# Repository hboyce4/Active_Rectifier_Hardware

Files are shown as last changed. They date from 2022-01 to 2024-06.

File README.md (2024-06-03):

Design files (Altium) for my bidirectional active rectifier. 

A Cortex-M4-driven bidirectional AC-DC power converter (active rectifier). 300W, 48VDC, 12VAC rms (through mains freq. step-down transformer). It should also be able to absorb/provide AC reactive power too. Its aim is more to be a test platform for control software than a useful/economical PSU. 

As of 2024-06-02, changes have been made to the inverter board but not incorporated into Altium because of a lack of license. They are:
 - PWModulator comparator output has been connected to GPIO PA.10 to measure duty cycle via a timer
 - U17, R56 and C87 have been removed as duty cycle is now measured digitally by a timer
 - R69 and R70 have been changed to 47 Ohm to improve rise time dramatically
 - R74, R76, R79 and R83 have all been changed to 1 Ohm to improve the power MOSFET's turn-off time

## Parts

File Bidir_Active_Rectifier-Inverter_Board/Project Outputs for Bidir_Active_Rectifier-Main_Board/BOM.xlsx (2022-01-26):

Comment | Description | Designator | Footprint | LibRef | Quantity | Value
GCM32EC71H106KA03L | CAP CER 10UF 50V X7S 1210 | C1, C2, C3, C4, C5, C15, C16, C17, C18, C19, C26, C74, C75, C102 | CAPC3225X27N | GCM32EC71H106KA03L | 14
CC0603KPX7R9BB104 | 0603 0.1 uF 50 V ±10% Tolerance X7R SMT Multilayer Ceramic Capacitor | C6, C7, C8, C20, C21, C22, C23, C24, C25, C30, C33, C34, C36, C38, C39, C40, C41, C42, C43, C44, C45, C50, C51, C53, C62, C64, C65, C70, C77, C79, C81, C90, C91, C92, C93, C94, C95, C96, C97, C98, C101, C103, C104, C105, C106, C107, C108, C110, C111 | CAPC1608X09N | CC0603KPX7R9BB104 | 49
GCM21BC7YA225KE02L | CAP CER 2.2UF 35V X7S 0805 | C9, C10, C11, C12, C13, C14, C27, C68, C69, C73, C80 | CAPC2012X14N | GCM21BC7YA225KE02L | 11
Cap | Capacitor | C28, C29 | CAPC2012X14N | Cap | 2 | 18 pF
Cap | Capacitor | C31, C32, C35, C37, C47 | CAPC1608X09N | Cap | 5 | 10 nF
Cap | Capacitor | C46, C87 | CAPC1608X09N | Cap | 2 | 1 nF
CL21A226KQCLRNC | Cap Ceramic 22uF 6.3V X5R 10% Pad SMD 0805 85°C T/R | C48, C49, C58, C59, C60, C61, C63, C66, C71 | CAPC2012X14N | CL21A226KQCLRNC | 9
CL31B475KAHNNNE | Ceramic capacitor SMD 1206 - 4700nF/25V, +-10%, X7R, Samsung, RoHS | C52, C78 | CAPC3216X12N | CL31B475KAHNNNE | 2
Cap | Capacitor | C54, C55 | CAPC1608X09N | Cap | 2
CL10A105KA5LNNC | Cap Ceramic 1uF 25V X5R 10% SMD 0603 85°C Cardboard T/R | C56, C76 | CAPC1608X09N | CL10A105KA5LNNC | 2
Cap | Capacitor | C57, C82 | CAPC1608X09N | Cap | 2 | 33 pF
35ZLJ330M8X20 | Cap Aluminum 330uF 35V 20% (8 X 20mm) Radial 3.5mm 1960mA 10000 hr 105°C Bulk | C67, C72 | ELECTROLYTIC_D8_P3.5_H20 | 35ZLJ330M8X20 | 2
Cap | Capacitor | C83, C84, C85, C86, C89 | CAPC2012X14N | Cap | 5 | 160 pF
Cap | Capacitor | C88 | CAPC2012X14N | Cap | 1 | 56 nF
Cap | Capacitor | C99 | CAPC2012X14N | Cap | 1 | 470 pF
GRM188R71E474KA12D | 0603 0.47 uF 25V ±10 % Tolerance X7R SMT Multilayer Ceramic Capacitor | C100, C112, C113 | CAPC1608X09N | GRM188R71E474KA12D | 3
Cap | Capacitor | C109 | CAPC2012X14N | Cap | 1 | 1 nF
150120RS75000 | LED RED CLEAR 1206 SMD | D1, D2, D3, D4, D11, D12 | 150120RS75000 | 150120RS75000 | 6
1N4007FLTR | Standard Rectifier 1000V SOD-123 | D5, D6, D7, D8, D9, D10 | SMC-Diodes-Solutions_SOD-123FL | 1N4007FLTR | 6
3529 | CLIP FUSE W/STOPS STR PC LEGS | F1 | 6.35x32mm_Glass_Fuse_3529_6A | 3529 | 1
7466204R | TERM PWR ELEMENT M4 1PIN SMD | J1, J2, J3, J6, J7, J8, J9 | 7466204R | 7466204R | 7
91601-306LF | FCI 2.54mm 6 Way 1 Row Straight PCB Socket Surface Mount Socket Strip | J4, J5 | 91601-306LF | 91601-306LF | 2
A11CSP12VDC1.2D | PC mount relay SPDT w/ diode | K1, K2 | CIT_A11xSP | A11CSP12VDC1.2D | 2
PA4349.472ANLT | Inductor Power Shielded/Molded Wirewound 4.7uH 20% 100KHz 47A 0.0022Ohm DCR Automotive T/R | L1 | Pulse_PA4349.XXXANLT | PA4349.472ANLT | 1
PE-0603PFB121ST | [NoValue], Ind Chip Bead Multi-Layer 470Ohm 25% 100MHz Ferrite 1.5A 0603 Paper T/R | L2, L4, L5, L6, L8 | INDC1608N | BLM18KG471SN1D | 5
CLF5030NIT-4R7N-D | Inductor Power Shielded Wirewound 4.7uH 30% 100KHz Ferrite 2.1A 0.078Ohm DCR Automotive T/R | L3 | TDK_CLF5030NIT | CLF5030NIT-4R7N-D | 1
ASPI-6045S-331M-T | Inductor Power Shielded Wirewound 330uH 20% 100KHz 0.57A 1.27Ohm DCR 2424 T/R | L7 | Abracon_ASPI-6045S | ASPI-6045S-331M-T | 1
CLF5030NIT-100M-D | Inductor Power Shielded Wirewound 10uH 20% 100KHz Ferrite 1.7A 0.114Ohm DCR Automotive T/R | L9 | TDK_CLF5030NIT | CLF5030NIT-100M-D | 1
Bourns SMD Indiuctor | Inductor Power Shielded Wirewound 10000uH 20% 100KHz 50Q-Factor Ferrite 0.02A 32.8Ohm DCR T/R | L10, L11 | SRE6603 | SRE6603-103M | 2
NCU18XH103F60RB | MURATA - NCU18XH103F60RB - Thermistor, NTC, 10 kohm, NCU Series, 3380 K, SMD, 0603 [1608 Metric] | NTC1 | RESC1608X06N | NCU18XH103F60RB | 1
NCU18XH103F60RB | MURATA - NCU18XH103F60RB - Thermistor, NTC, 10 kohm, NCU Series, 3380 K, SMD, 0603 [1608 Metric] | NTC2 | RESC3216X06N | NCU18XH103F60RB | 1
TLP176D(F) | MOSFET Output Optocouplers Photorelay Voff=200V Ion=0.2A | OP1, OP2, OP3, OP4 | Toshiba_2.54SOP4_11-5H1 | TLP176D(F) | 4
10129383-904001BLF | Conn Unshrouded Header HDR 4 POS 2.54mm Solder ST SMD Poly Bag | P1 | 10129383-904001BLF | 10129383-904001BLF | 1
10129383-910001ALF | Conn Unshrouded Header HDR 10 POS 2.54mm Solder ST SMD T/R | P2 | 10129383-910001ALF | 10129383-910001ALF | 1
PFMF.010.2 | PTC Resettable Fuse 0.1A(hold) 0.3A(trip) 60VDC 40A 0.8W 1.5s 0.7Ohm SMD Solder Pad 1812 T/R | PTC1, PTC2 | 0ZCG0_BEL_FUSE | PFMF.010.2 | 2
BSZ110N08NS5ATMA1 | BSZ110N08NS5 Series 80 V 40 A OptiMOSTM5 Power-Transistor - PG-TSDSON-8 FL | Q1, Q2, Q3, Q4 | INFINEON_PG-TSDSON-8-32 | BSZ110N08NS5ATMA1 | 4
RL1632T4F-R004-FNH | Fixed Resistor, Metal Foil, 1W, 0.004ohm, 0.0632V, 1% +/-Tol, 100ppm/Cel, Surface Mount, 0613 | R1, R2 | RESC3216X06N | RL1632T4F-R004-FNH | 2 | 4 mΩ
Res1 | Resistor | R3, R4, R33, R34, R36, R59, R60, R61, R63, R64, R65, R66, R77, R85, R89 | RESC1608X06N | Res1 | 15 | 100K
Res1 | Resistor | R5, R14, R19, R23, R25, R28, R58, R68, R84, R90 | RESC1608X06N | Res1 | 10 | 10K
Res1 | Resistor | R6, R7, R8, R9, R18, R26, R30 | RESC1608X06N | Res1 | 7 | 750R
Res1 | Resistor | R10, R20, R56 | RESC1608X06N | Res1 | 3 | 27K
Res1 | Resistor | R11, R13 | RESC1608X06N | Res1 | 2 | 6K2
Res1 | Resistor | R12 | RESC1608X06N | Res1 | 1 | 3K
Res1 | Resistor | R15, R22 | RESC1608X06N | Res1 | 2 | 3K6
Res1 | Resistor | R16 | RESC1608X06N | Res1 | 1 | 1K3
Res1 | Resistor | R17, R24 | RESC1608X06N | Res1 | 2 | 43K
Res1 | Resistor | R21, R69, R72, R87 | RESC1608X06N | Res1 | 4 | 1K
Res1 | Resistor | R27, R29 | RESC1608X06N | Res1 | 2 | 2K7
Res1 | Resistor | R31 | RESC1608X06N | Res1 | 1 | 52K5
Res1 | Resistor | R32, R43, R80, R82, R86, R91, R92, R94, R95 | RESC1608X06N | Res1 | 9 | 15K
Res1 | Resistor | R35 | RESC1608X06N | Res1 | 1 | 100R
Res1 | Resistor | R37, R62 | RESC1608X06N | Res1 | 2 | 51K
Res1 | Resistor | R38, R40 | RESC3216X06N | Res1 | 2 | 1K5
Res1 | Resistor | R39 | RESC3216X06N | Res1 | 1 | 10K
Res1 | Resistor | R41 | RESC1608X06N | Res1 | 1 | 2K
Res1 | Resistor | R42 | RESC1608X06N | Res1 | 1 | 180K
Res1 | Resistor | R44, R45, R46, R47, R48, R49, R54, R55 | RESC1608X06N | Res1 | 8 | 330R
RMCF2512JT100R | Res Thick Film 2512 100 Ohm 5% 1W ±200ppm/C Molded SMD Automotive T/R | R50, R51, R52, R53 | RESC6432N | RMCF2512JT100R | 4
Res1 | Resistor | R57 | RESC1608X06N | Res1 | 1 | 33K
Res1 | Resistor | R67 | RESC1608X06N | Res1 | 1 | 5K1
Res1 | Resistor | R70, R88 | RESC1608X06N | Res1 | 2 | 0R
Res1 | Resistor | R71 | RESC1608X06N | Res1 | 1 | 4K3
Res1 | Resistor | R73, R74, R75, R76, R78, R79, R81, R83 | RESC1608X06N | Res1 | 8 | 4R3
Res1 | Resistor | R93 | RESC1608X06N | Res1 | 1 | 300K
Res1 | Resistor | R96, R97 | RESC1608X06N | Res1 | 2 | 220R
ZMA03A150P00PC | Switch Snap Action N.O./N.C. SPDT Pin Plunger 3A 125VAC 24VDC 1.47N Thru-Hole PC Pins Bulk | SW1 | ZMAxxxxxxP00P | ZMA03A150P00PC | 1
Test_Point_0.8mm |  | TP1, TP2, TP3, TP4, TP5, TP6, TP7, TP8, TP9 | TEST_POINT_0.8mm | Test_Point_0.8mm | 9
SMCJ30A | SMCJ Series 1.5 kW 30 V Uni-Directional Surface Mount TVS Diode - DO-214AB | TVS1, TVS2, TVS5, TVS6 | Littelfuse_DO-214AB | SMCJ30A | 4
SMCJ20CA | Diode TVS Single Bi-Dir 20V 1.5KW 2-Pin DO-214AB T/R | TVS3, TVS4 | Littelfuse_DO-214AB _BIDIR | SMCJ20CA | 2
ISO7710FDR | Robust EMC, single-channel, reinforced digital isolator 8-SOIC -55 to 125 | U1, U2, U23, U26 | TI_SOIC-8_D0008A | ISO7710FDR | 4
M481LIDAE | Nuvoton Cortex-M4 160K RAM 512K Flash 48LQFP | U3 | Nuvoton_LQFP_48L_M | M481LIDAE | 1
MCP6L01T-E/OT | MCP6L01 Series 6 V 1 MHz Rail-to-Rail I/O Operational Amplifier - SOT-23-5 | U4, U5, U6, U7, U10, U11, U14, U17 | ANALOG_DEVICE_TSOT-23-5_UJ-5 | MCP6L01T-E/OT | 8
AD8615AUJZ-R2 | Op Amp Single Precision Amplifier R-R I/O 5V 5-Pin TSOT T/R | U8, U9, U18, U19, U20 | ANALOG_DEVICE_TSOT-23-5_UJ-5 | AD8615AUJZ-R2 | 5
S-8580AA-A6T8U7 | IC Reg Buck Adj 600MA HSNT-8(203 | U12, U15 | ABLIC_HSNT-6 | S-8580AA-A6T8U7 | 2
MAX8877EUK33+T | MAX8877 Series 3.3 V 150 mA Fixed Low-Dropout Linear Regulator - SOT-23-5 | U13 | MAXIM_SOT23-5 | MAX8877EUK33+T | 1
AS78L05RTR-E1 | IC REG LINEAR 5V 100MA SOT89-3 | U16 | SOT89N | AS78L05RTR-E1 | 1
TS5A4594DCKR | 5-V, 1: 1 (SPST), 1-channel general-purpose analog switch (active high) 5-SC70 -40 to 85 | U21 | TI_SC70_M | TS5A4594DCKR | 1
TLV3501AIDBVR | 4.5ns, Rail-to-Rail, High Speed Comparator with Shutdown 6-SOT-23 -40 to 125 | U22 | TI_SOT-23-6_DBV0006A | TLV3501AIDBVR | 1
MAX9140EUK+T | MAX9140 Series 5.5 V 320 nA SMT Single General Purpose Comparator - SOT-23-5 | U24, U28, U30 | MAXIM_SOT23-5 | MAX9140EUK+T | 3
ISL78424AVEZ-T7A | 100V Boot, 4A Peak, Half-Bridge Driver with Single PWM Input and Adaptive Dead Time Control | U25 | RENESAS_14-HTSSOP_M14.173B | ISL78424AVEZ-T7A | 1
SN74LVC1G123DCTR | Single retriggerable monostable multivibrator with Schmitt-trigger inputs 8-SM8 -40 to 125 | U27 | TI_SSOP-8_DCT0008A_M | SN74LVC1G123DCTR | 1
SN74LVC02APW | 4-ch, 2-input, 1.5-V to 3.6-V NOR gates 14-TSSOP -40 to 125 | U29 | TI_PW_TSSOP-14 | SN74LVC02APW | 1
FA-238A 12MHz | CRYSTAL 12.00 MHZ 18.0PF SMD | XTAL1 | Epson_FA-238V | FA-238A 12MHz | 1

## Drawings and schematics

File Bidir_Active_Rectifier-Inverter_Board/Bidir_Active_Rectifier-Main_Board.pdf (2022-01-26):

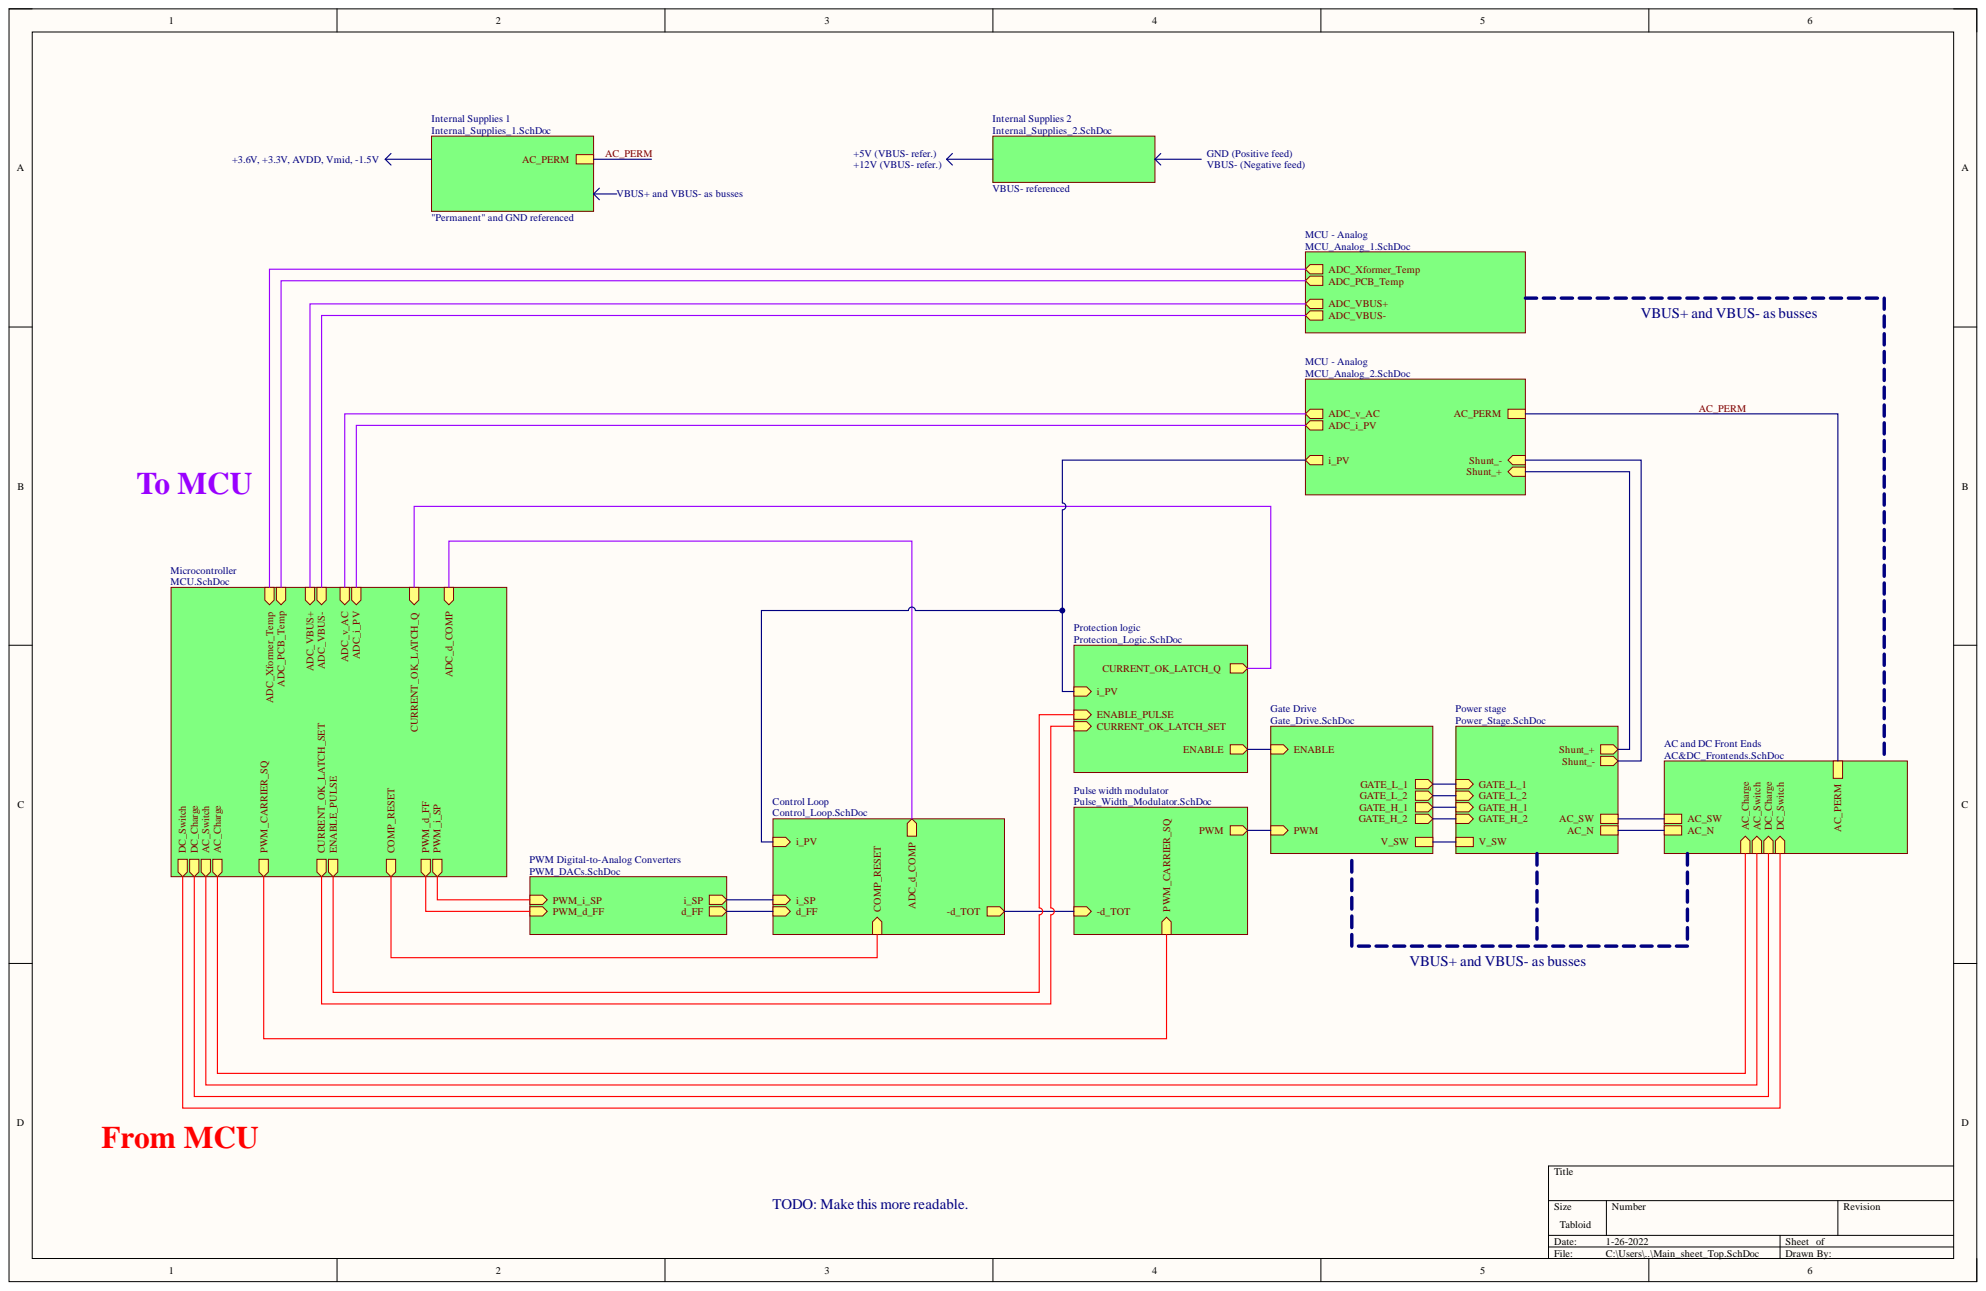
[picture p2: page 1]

+12V (VBUS- refer.) +3.6V, +3.3V, AVDD, Vmid, -1.5V

VBUS+ and VBUS- as busses

"Permanent" and GND referenced

AC and DC Front Ends

PWM Digital-to-Analog Converters PWM_DACs.SchDoc

PWM_i_SP i_SP PWM_d_FF d_FF | i_SP | -d_TOT | -d_TOT

TODO: Make this more readable.

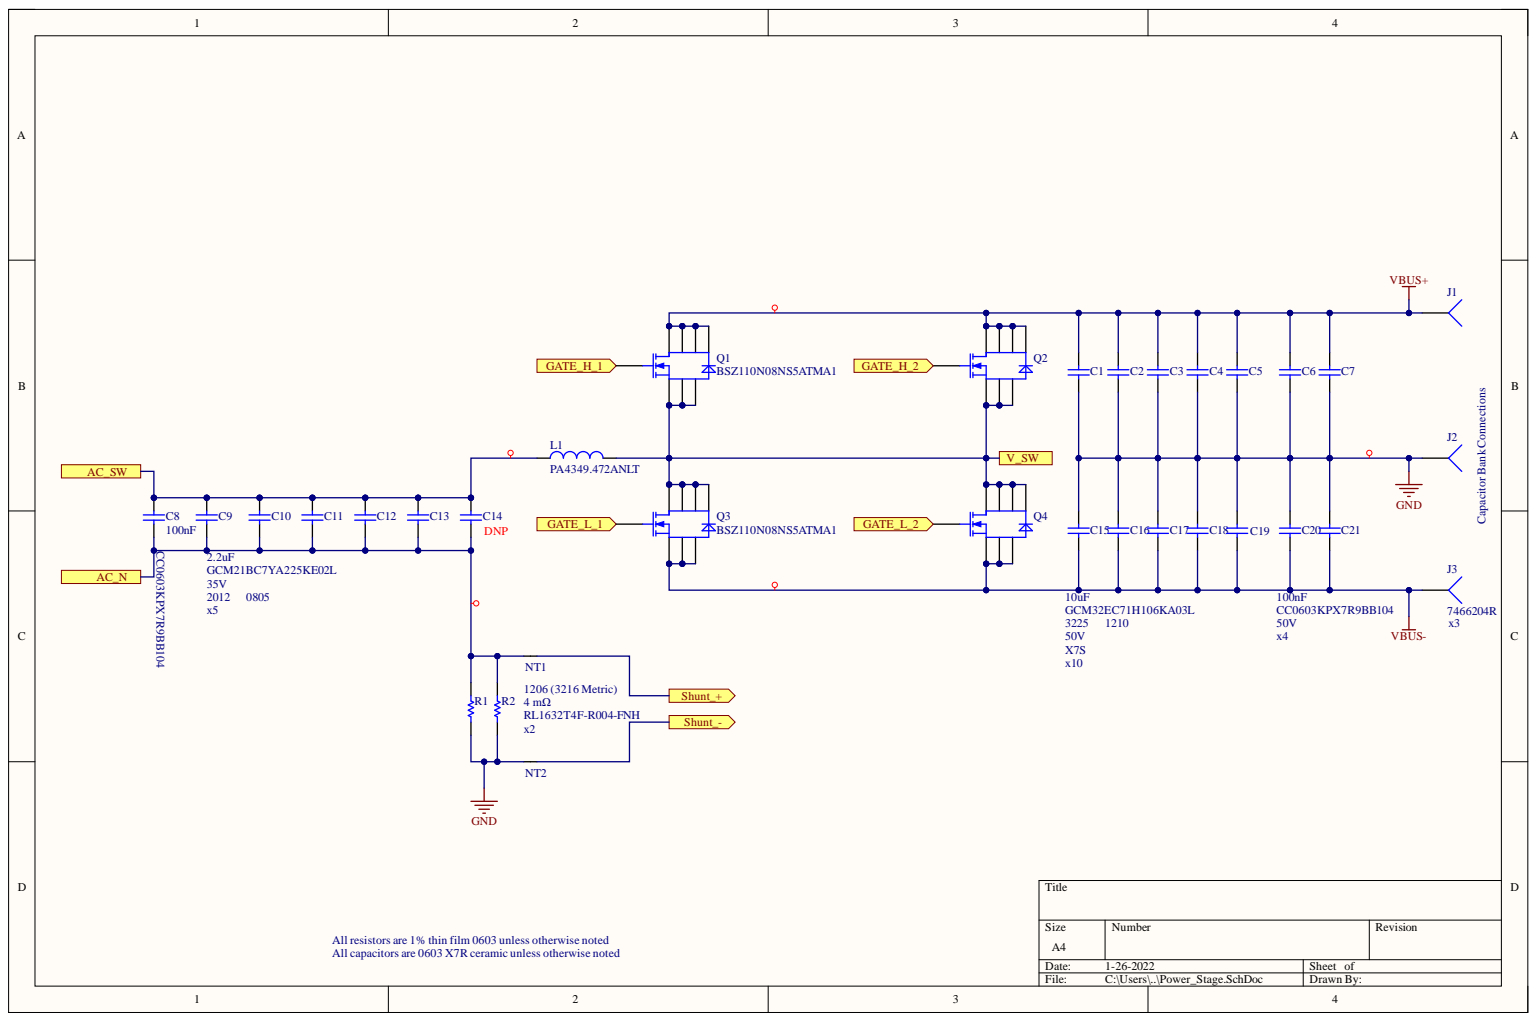
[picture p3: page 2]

All resistors are 1% thin film 0603 unless otherwise noted
All capacitors are 0603 X7R ceramic unless otherwise noted

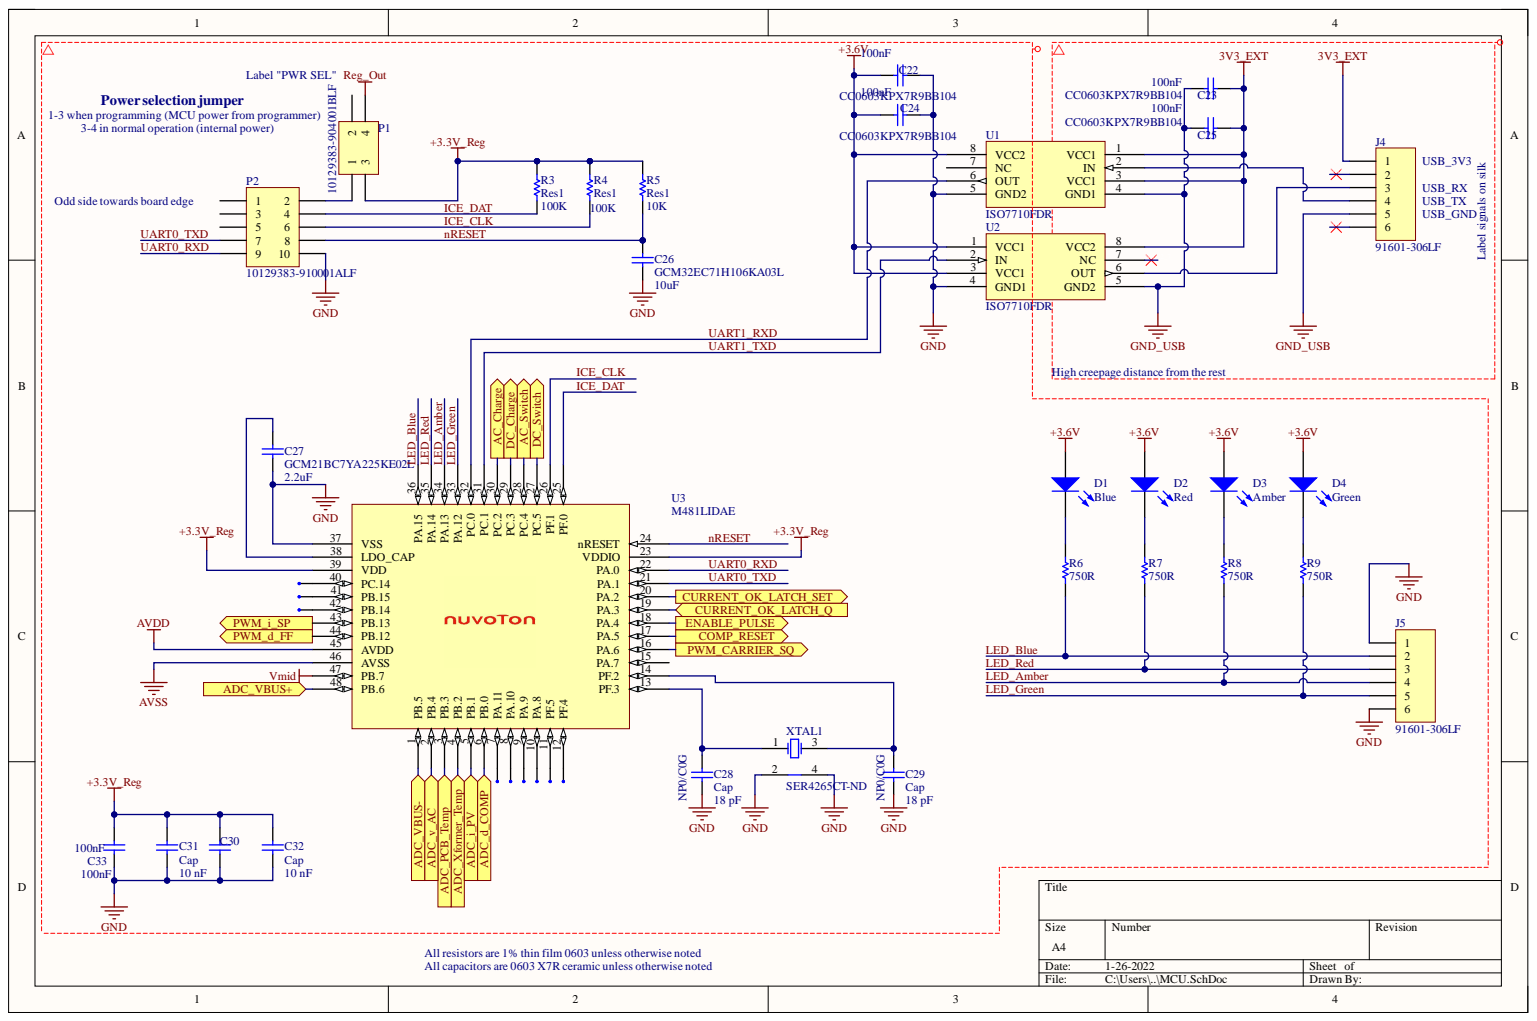
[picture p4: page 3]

1-3 when programming (MCU power from programmer)
3-4 in normal operation (internal power)

Label signals on silk

ICE_DAT Odd side towards board edge

High creepage distance from the rest

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

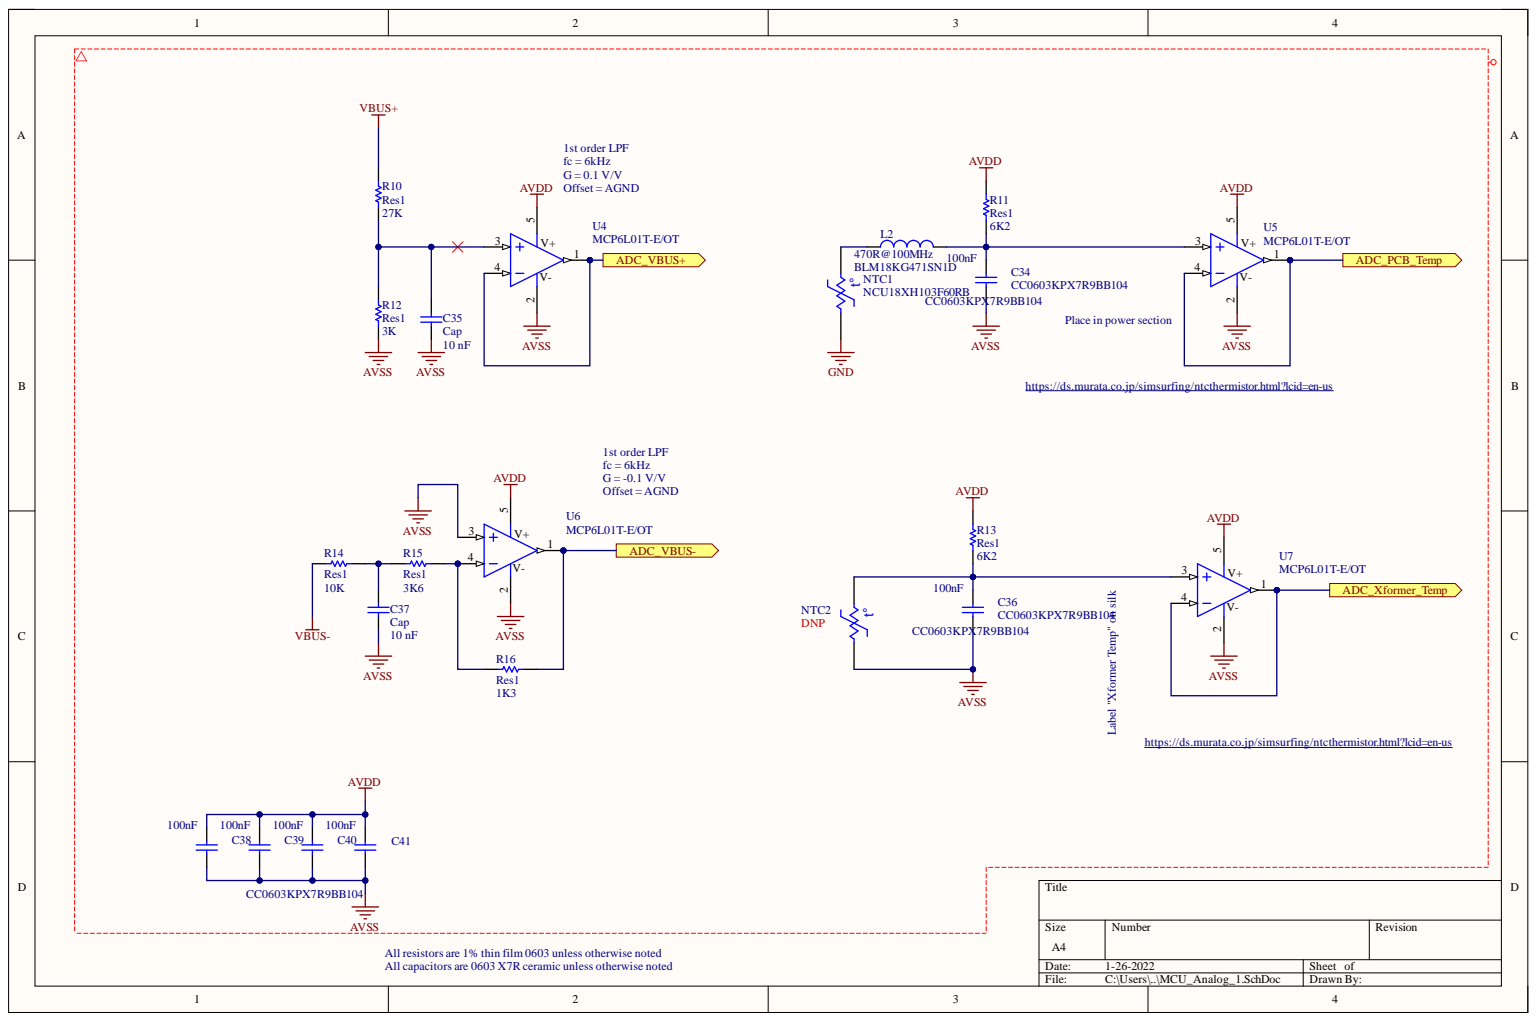
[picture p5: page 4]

Place in power section

https://ds.murata.co.jp/simsurfing/ntcthermistor.html?lcid=en-us

Label "Xformer Temp" on silk

All resistors are 1% thin film 0603 unless otherwise noted

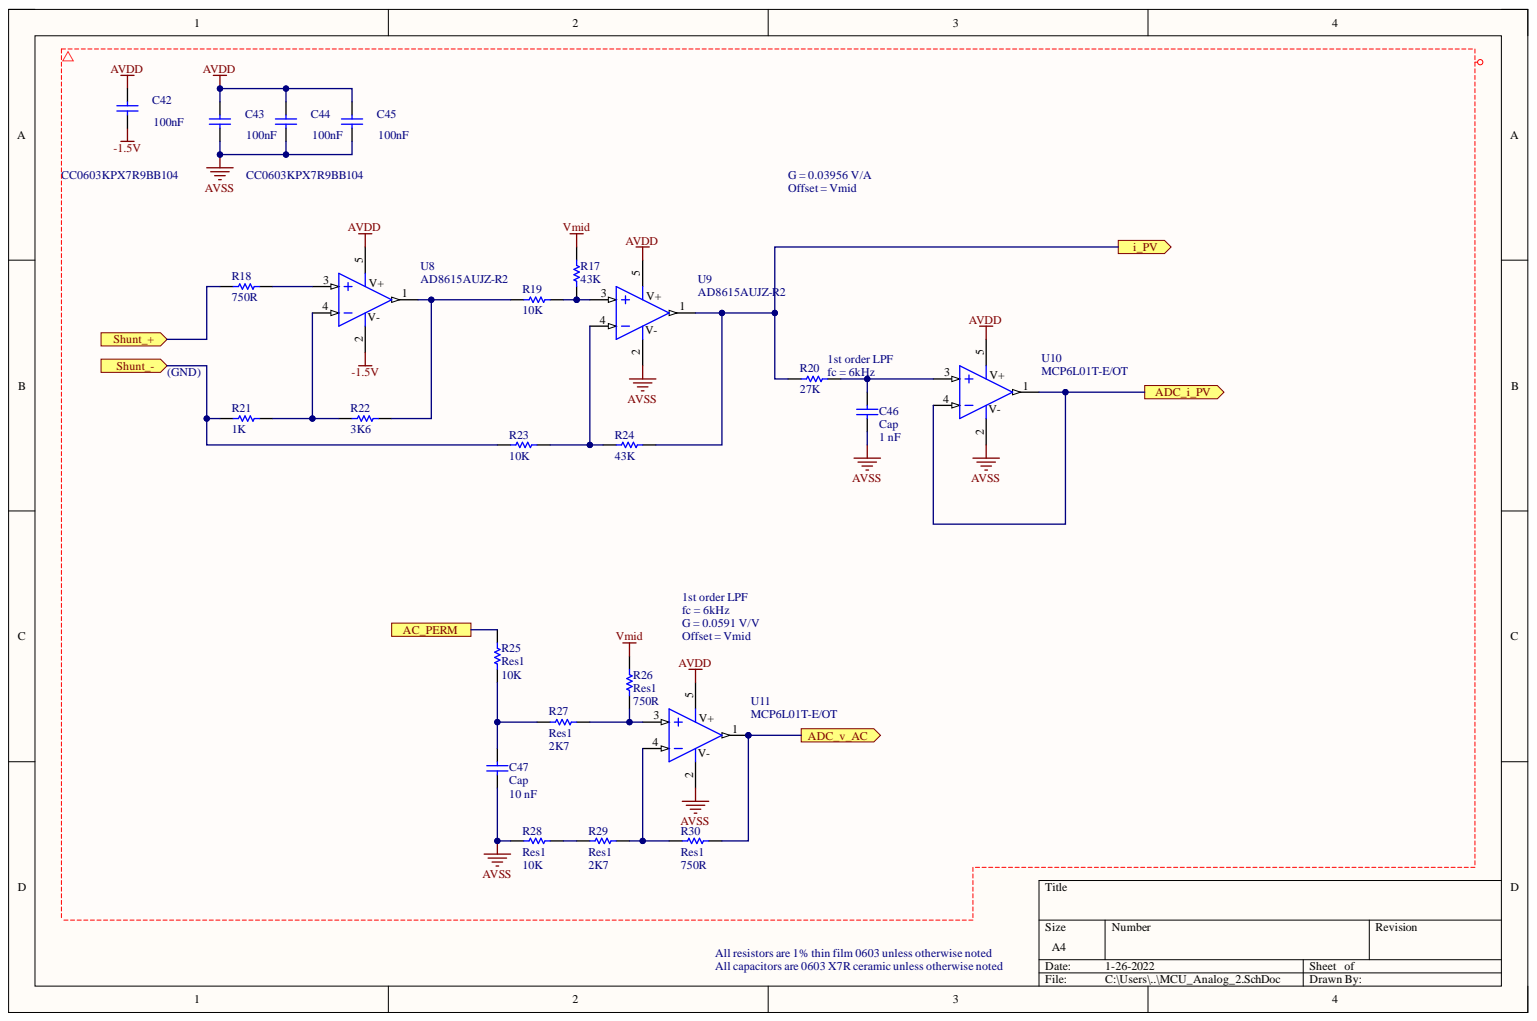
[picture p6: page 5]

All resistors are 1% thin film 0603 unless otherwise noted

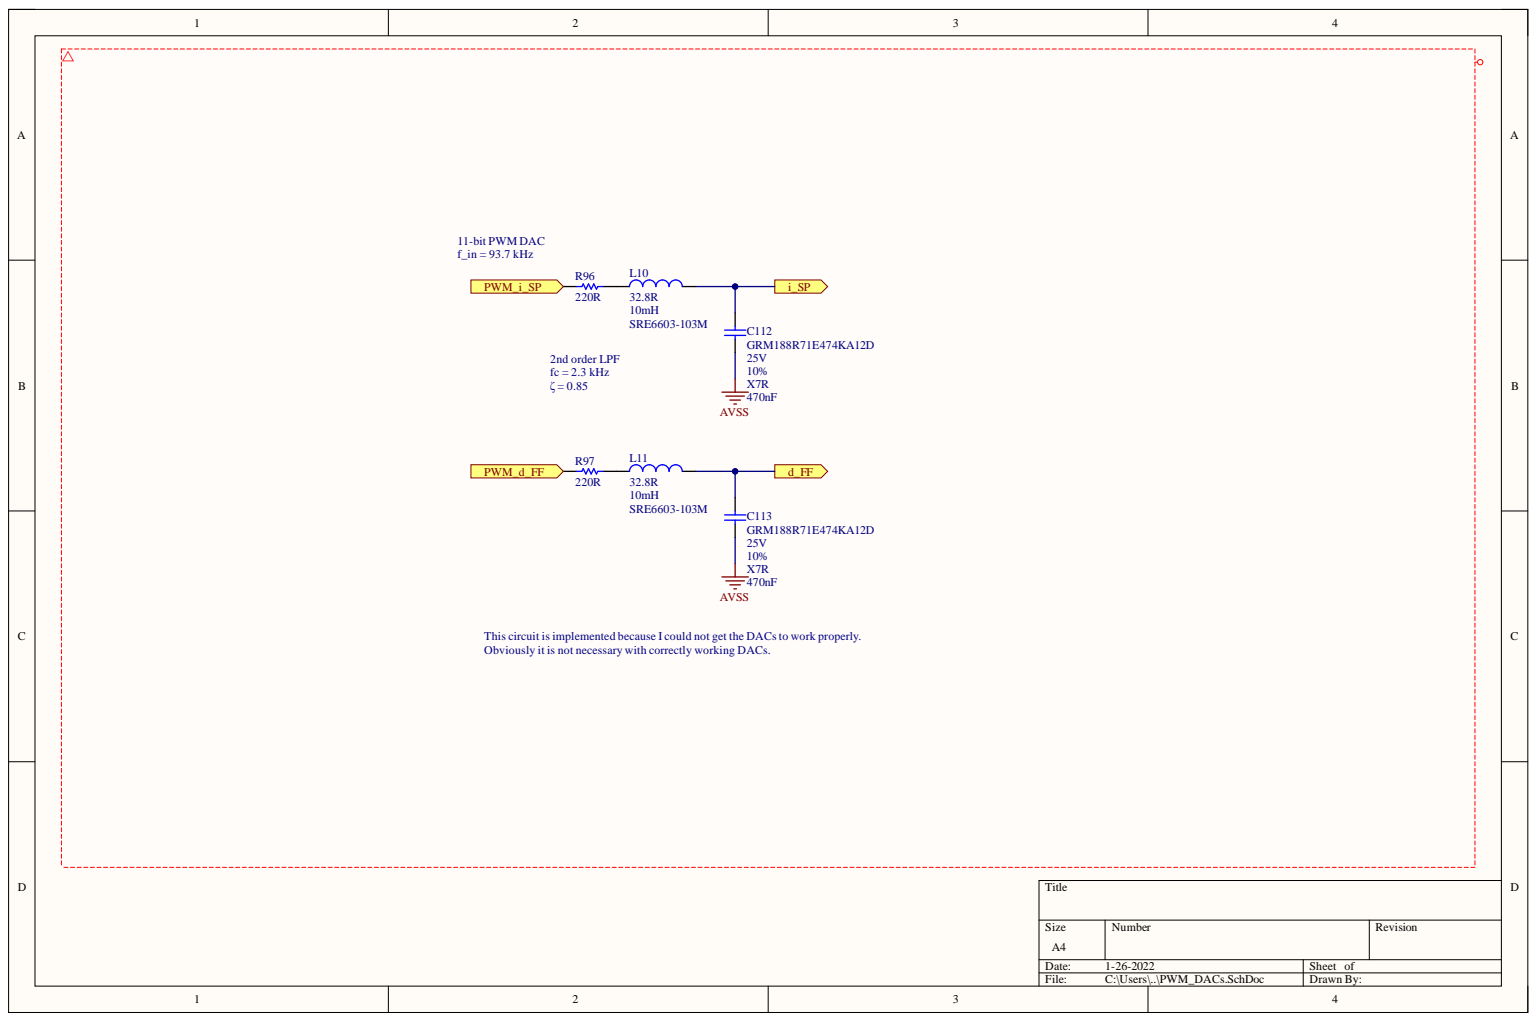
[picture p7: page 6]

This circuit is implemented because I could not get the DACsto work properly.
Obviously it is not necessary with correctly working DACs.

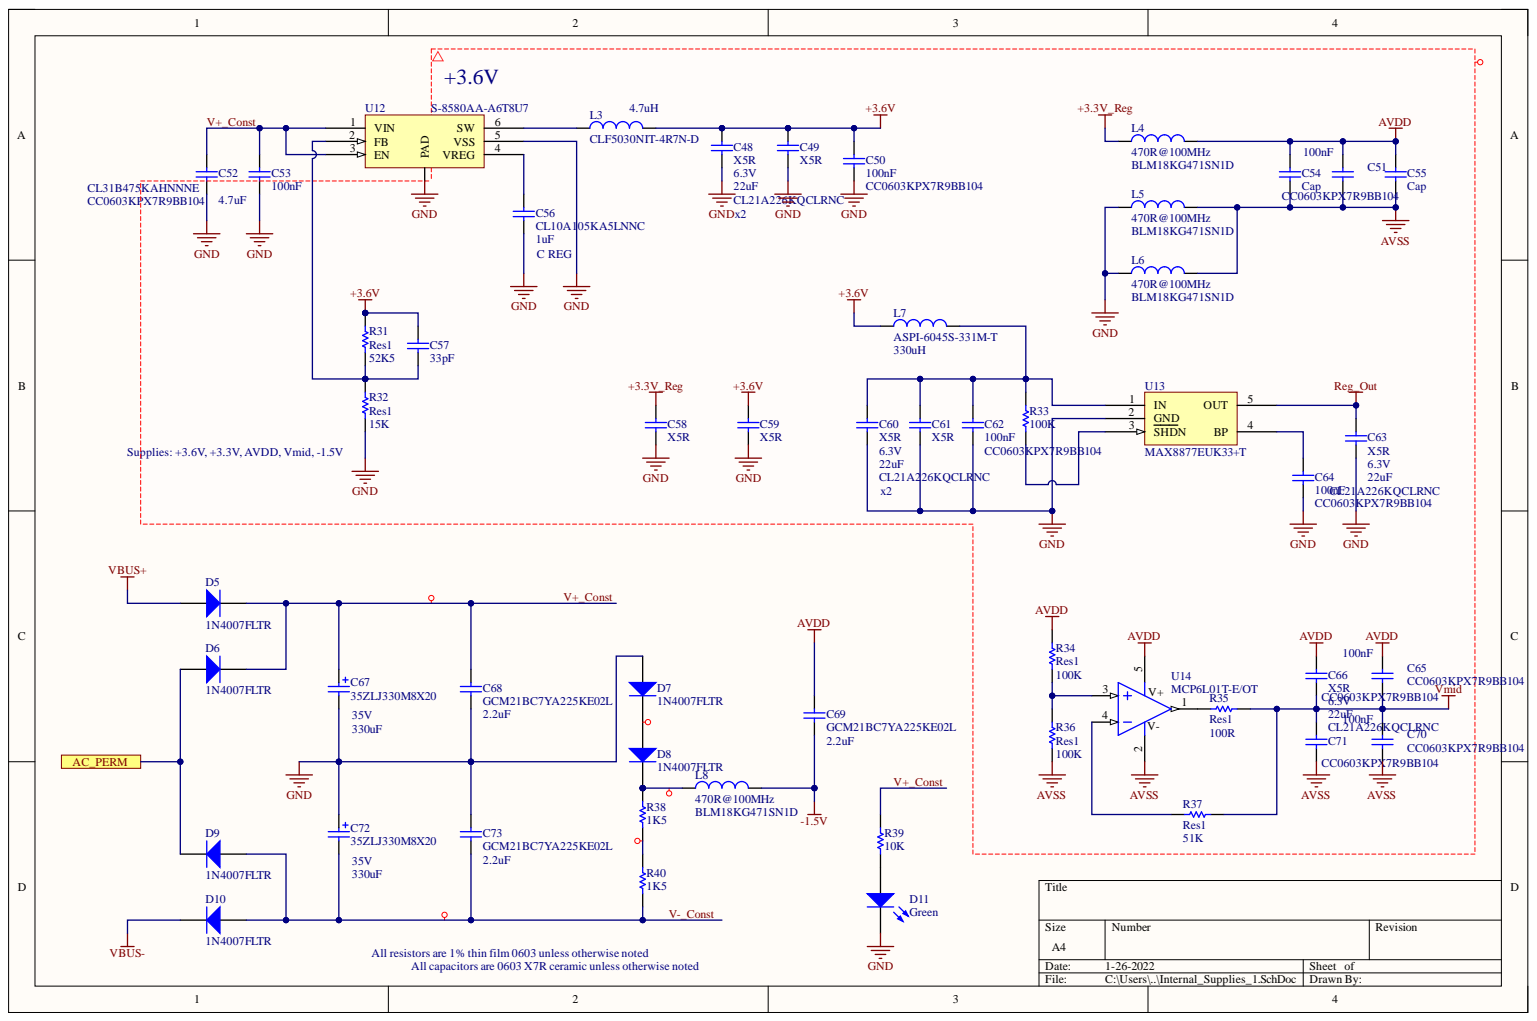
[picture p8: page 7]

3 | | 4 | C5 6 CL 1 0 A 1 1 u F C RE G

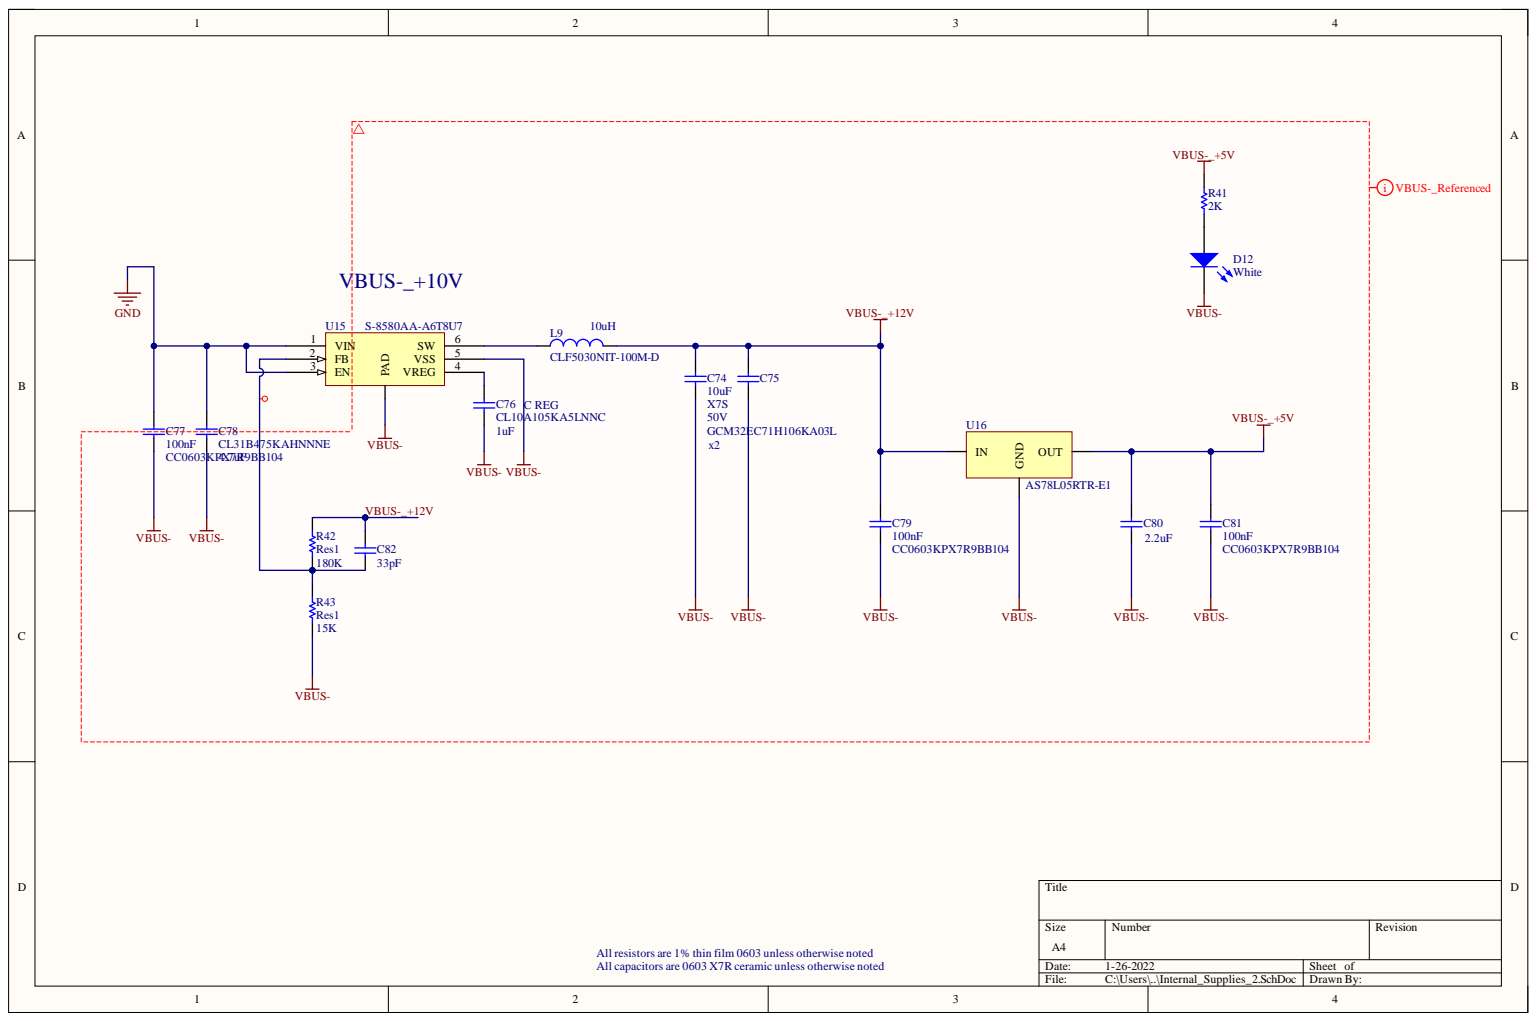
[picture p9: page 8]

3 | | 4 | C7 CL 1 0 1 u F

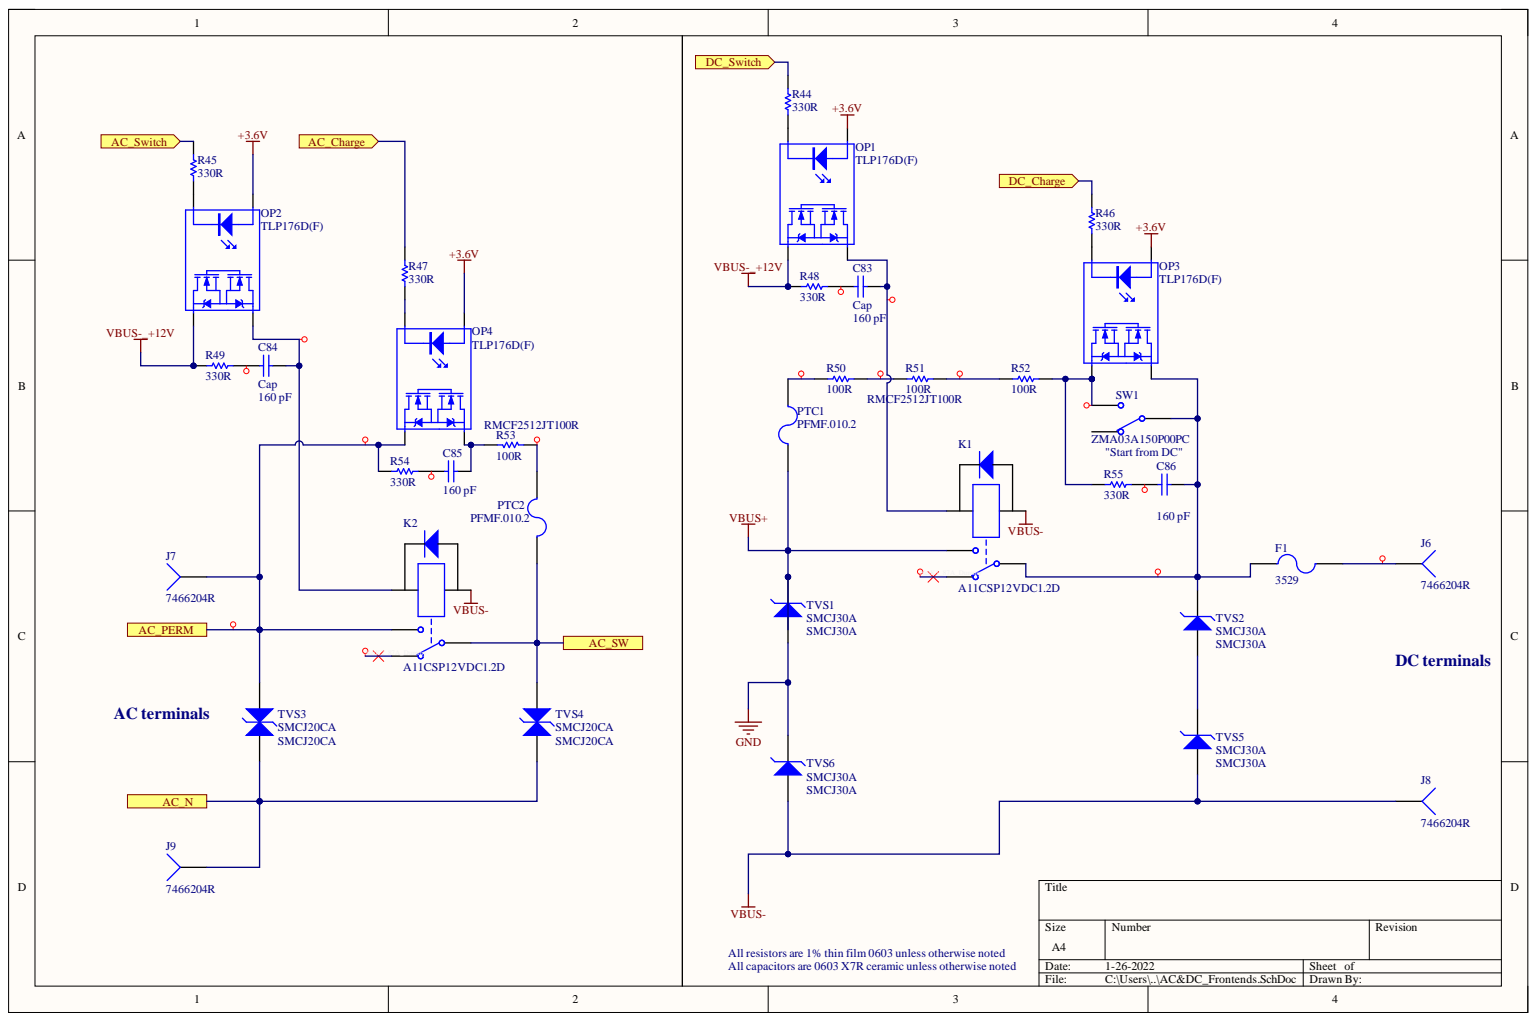
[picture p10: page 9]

All resistors are 1% thin film 0603 unless otherwise noted

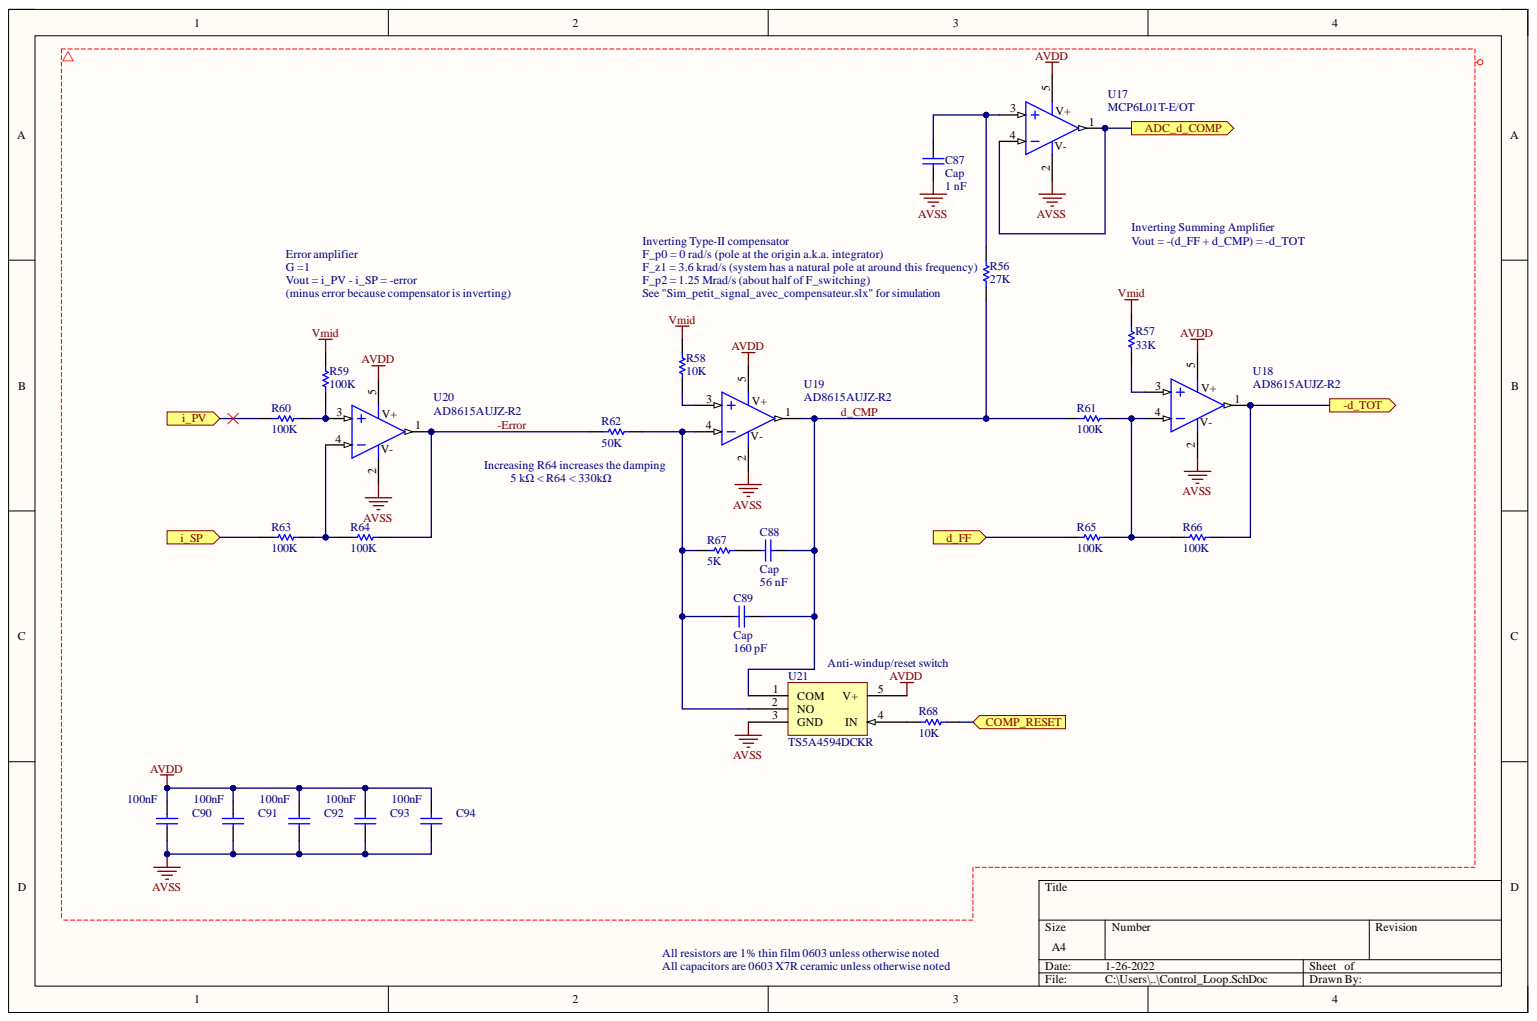
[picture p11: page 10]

AVDD

4 | AVSS

Inverting Type-II compensator
F_p0 = 0 rad/s (pole at the origin a.k.a. integrator)
F_z1 = 3.6 krad/s (system has a natural pole at around this frequency)
F_p2 = 1.25 Mrad/s (about half of F_switching)
See "Sim_petit_signal_avec_compensateur.slx" for simulation

Error amplifier
Vout = i_PV - i_SP = -error
(minus error because compensator is inverting)

Increasing R64 increases the damping

Anti-windup/reset switch

All resistors are 1% thin film 0603 unless otherwise noted

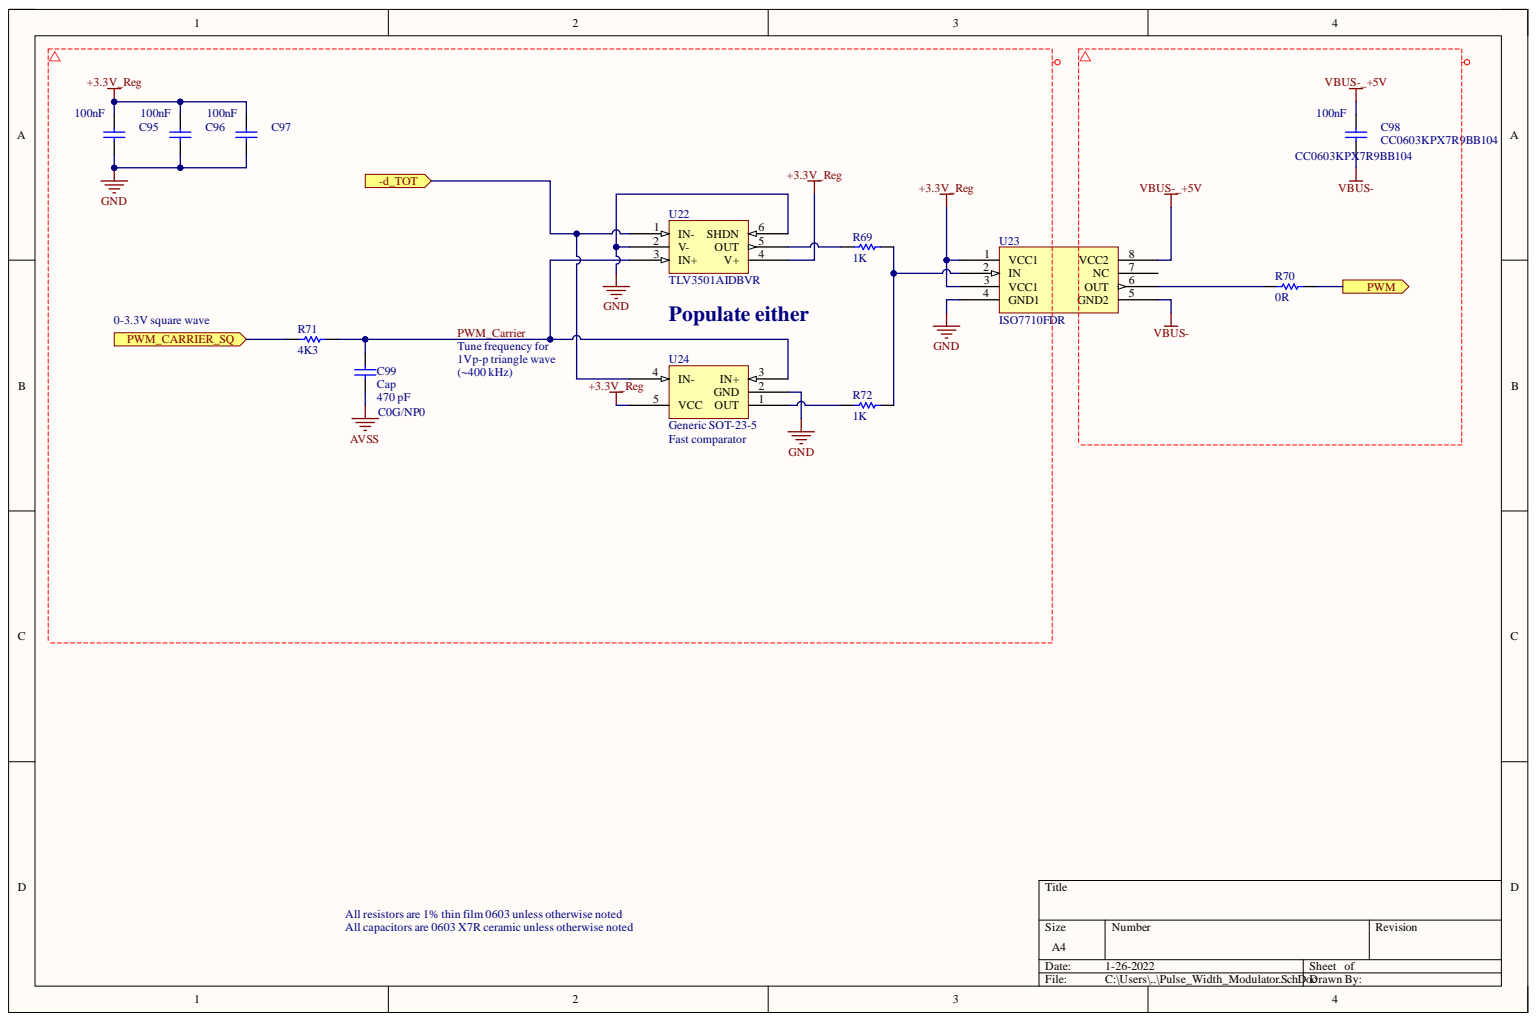
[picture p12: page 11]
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

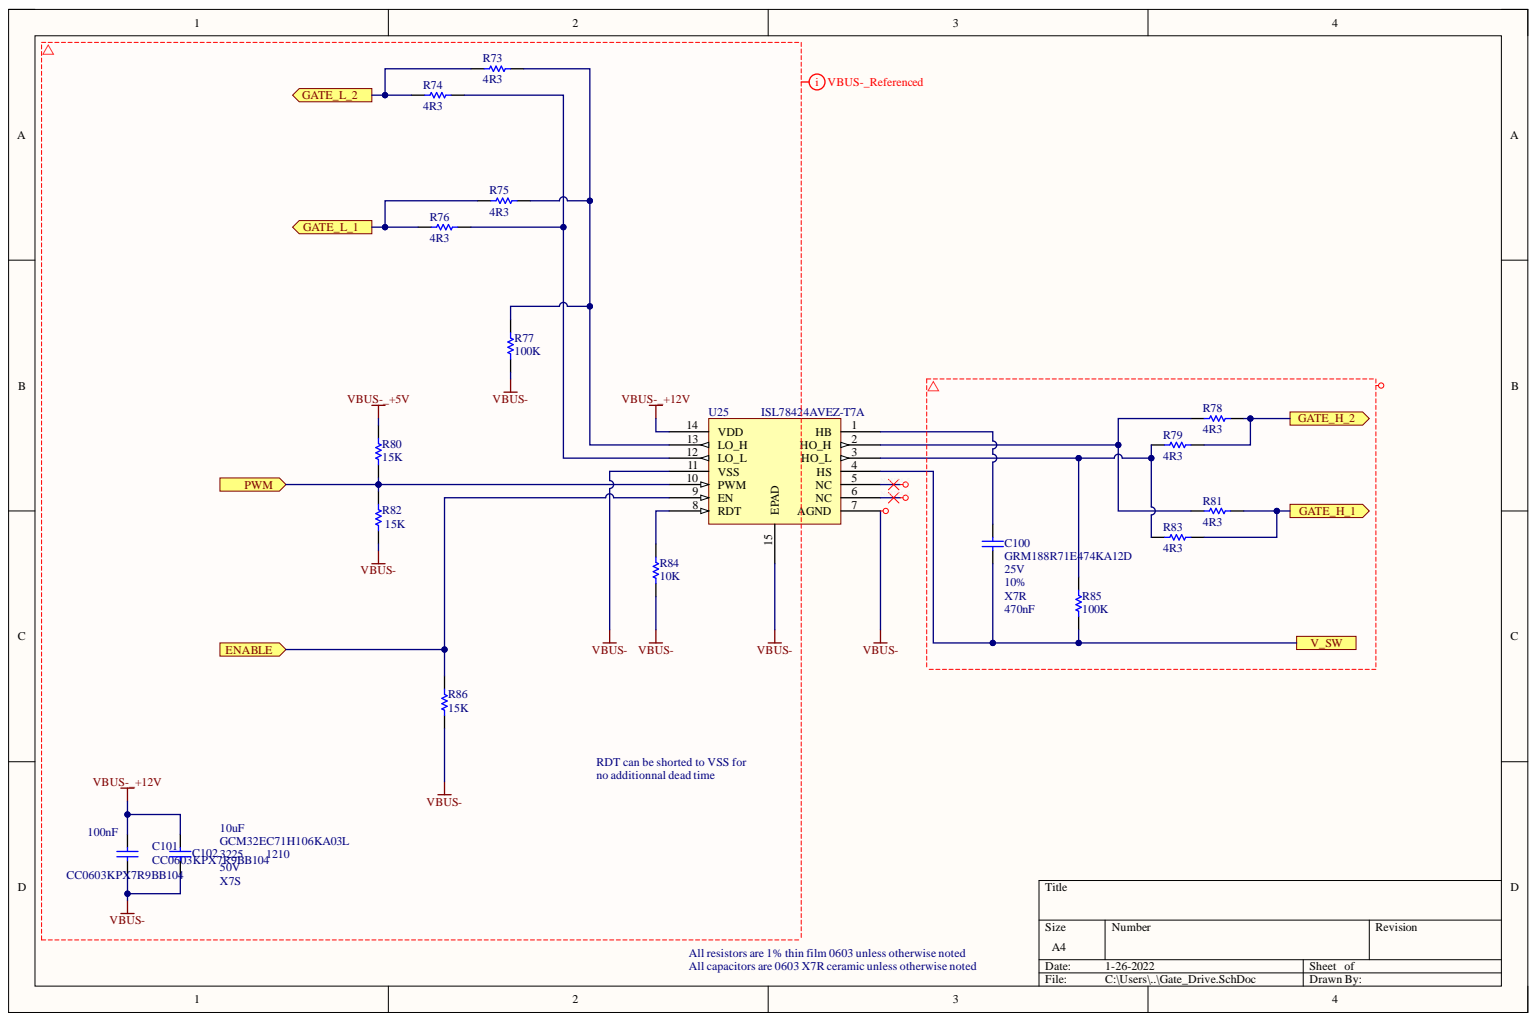
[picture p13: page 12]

RDT can be shorted to VSS for
no additionnal dead time

All resistors are 1% thin film 0603 unless otherwise noted


Trigger on rising edge
100 μs pulse duration
Retriggerable

Rising edge at most every 100 μs
to enable gate driver.

ENABLE_PULSE has to be LOW when the
latch is set, otherwise trigerring will occur.


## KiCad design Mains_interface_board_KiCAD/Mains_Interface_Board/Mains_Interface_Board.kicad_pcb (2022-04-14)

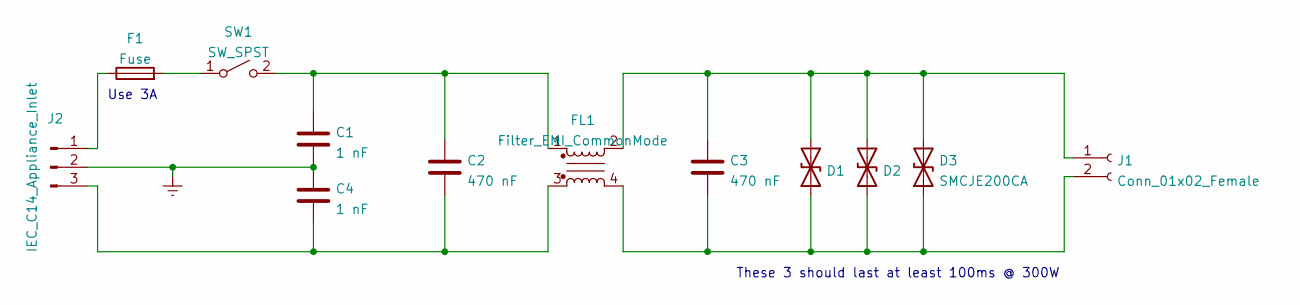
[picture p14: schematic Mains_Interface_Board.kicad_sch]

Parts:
C1, C4: 1 nF; C_Disc_D8.0mm_W5.0mm_P10.00mm
C2, C3: 470 nF; C_Rect_L26.5mm_W10.5mm_P22.50mm_MKS4
D1, D2, D3: SMCJE200CA; D_SMC
F1: Fuse; Fuseholder_Cylinder-6.3x30mm_Dual_Clips_Horizontal
FL1: Filter_EMI_CommonMode; Common_Mode_Choke_14x15mm
J1: Conn_01x02_Female; Dual_spades
J2: IEC_C14_Appliance_Inlet
SW1: SW_SPST; Dual_spades

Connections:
Earth: C1.2, C4.1, J2.2
unnamed: C1.1, C2.1, FL1.1, SW1.2 (B)
unnamed: C2.2, C4.2, FL1.3, J2.3
unnamed: C3.1, D1.2 (A2), D2.2 (A2), D3.2 (A2), FL1.2, J1.1
unnamed: C3.2, D1.1 (A1), D2.1 (A1), D3.1 (A1), FL1.4, J1.2
unnamed: F1.1, J2.1
unnamed: F1.2, SW1.1 (A)

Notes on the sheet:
Use 3A
These 3 should last at least 100ms @ 300W

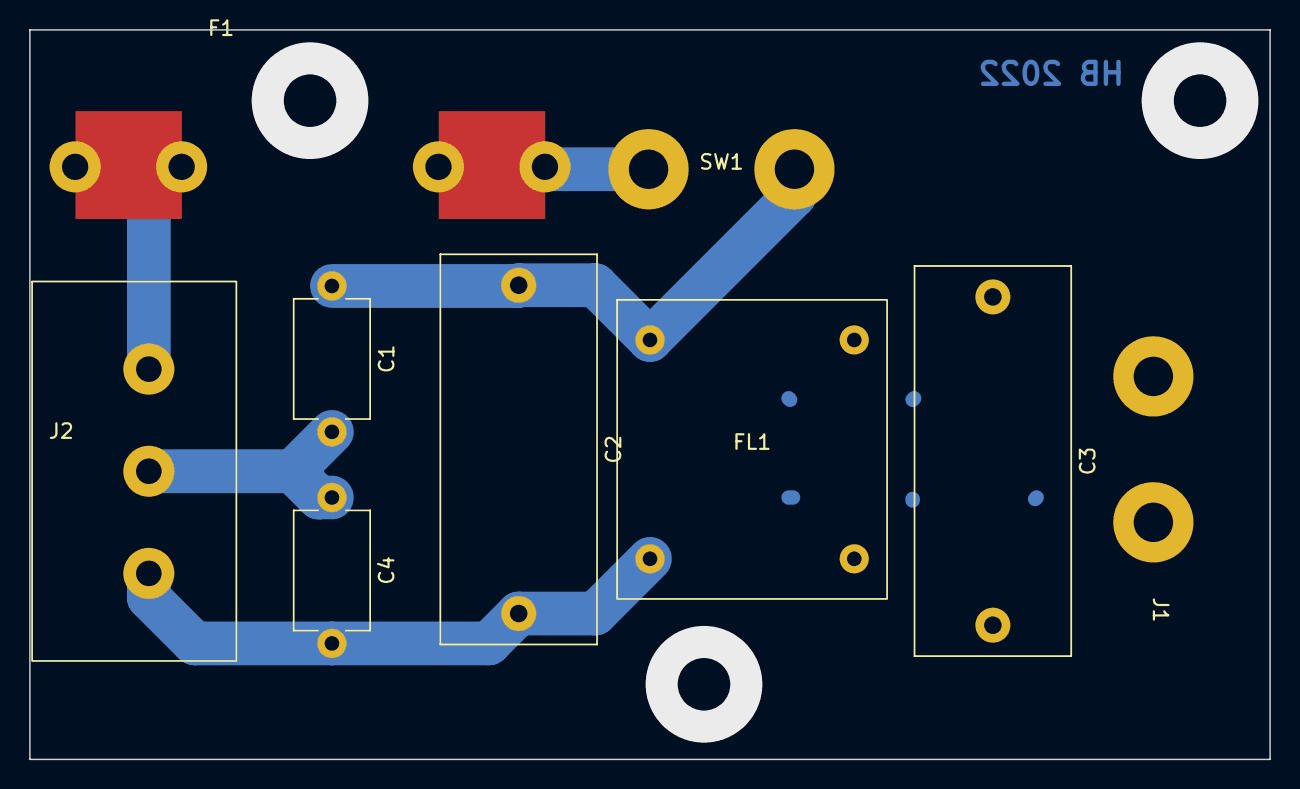
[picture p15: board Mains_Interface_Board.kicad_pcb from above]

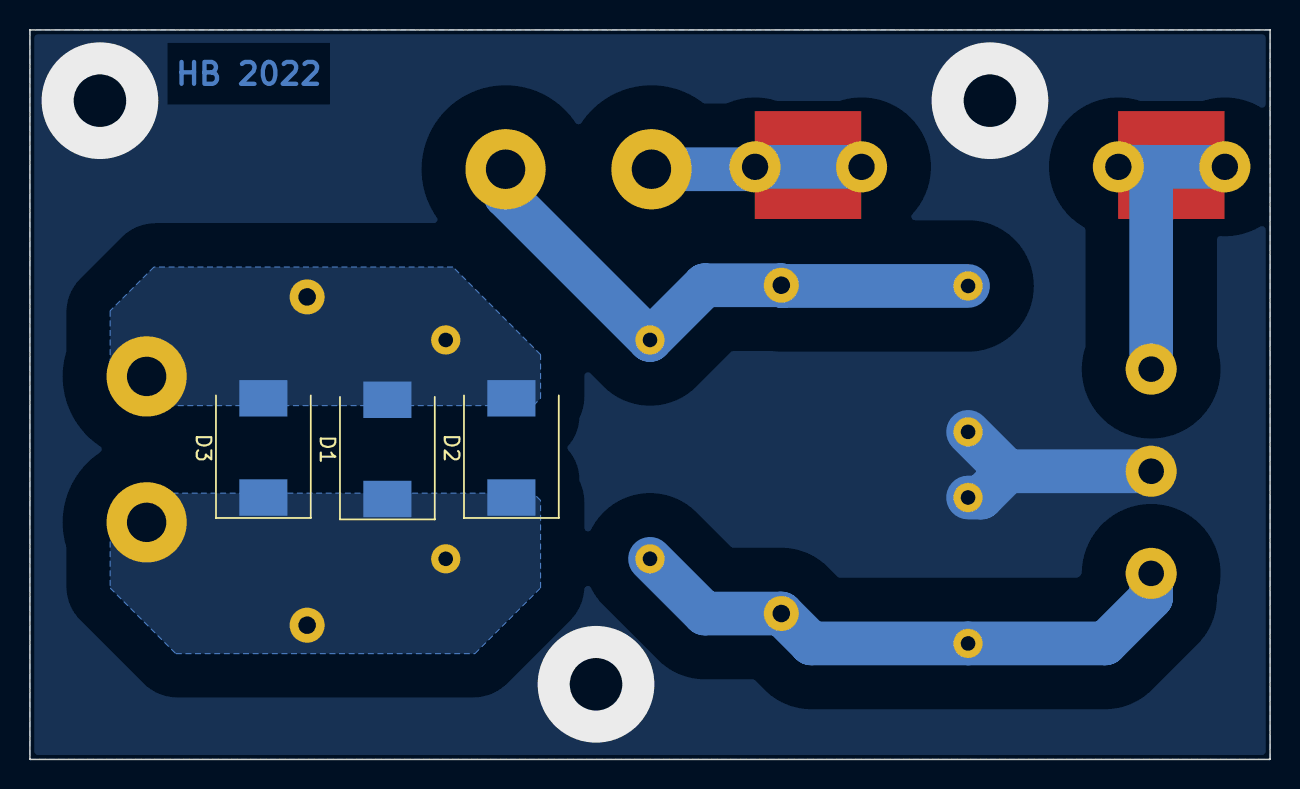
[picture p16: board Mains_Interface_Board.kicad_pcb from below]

Board: 2 copper layers, 85.0 x 50.0 mm, 12 parts (3 on the bottom side), 7 nets.

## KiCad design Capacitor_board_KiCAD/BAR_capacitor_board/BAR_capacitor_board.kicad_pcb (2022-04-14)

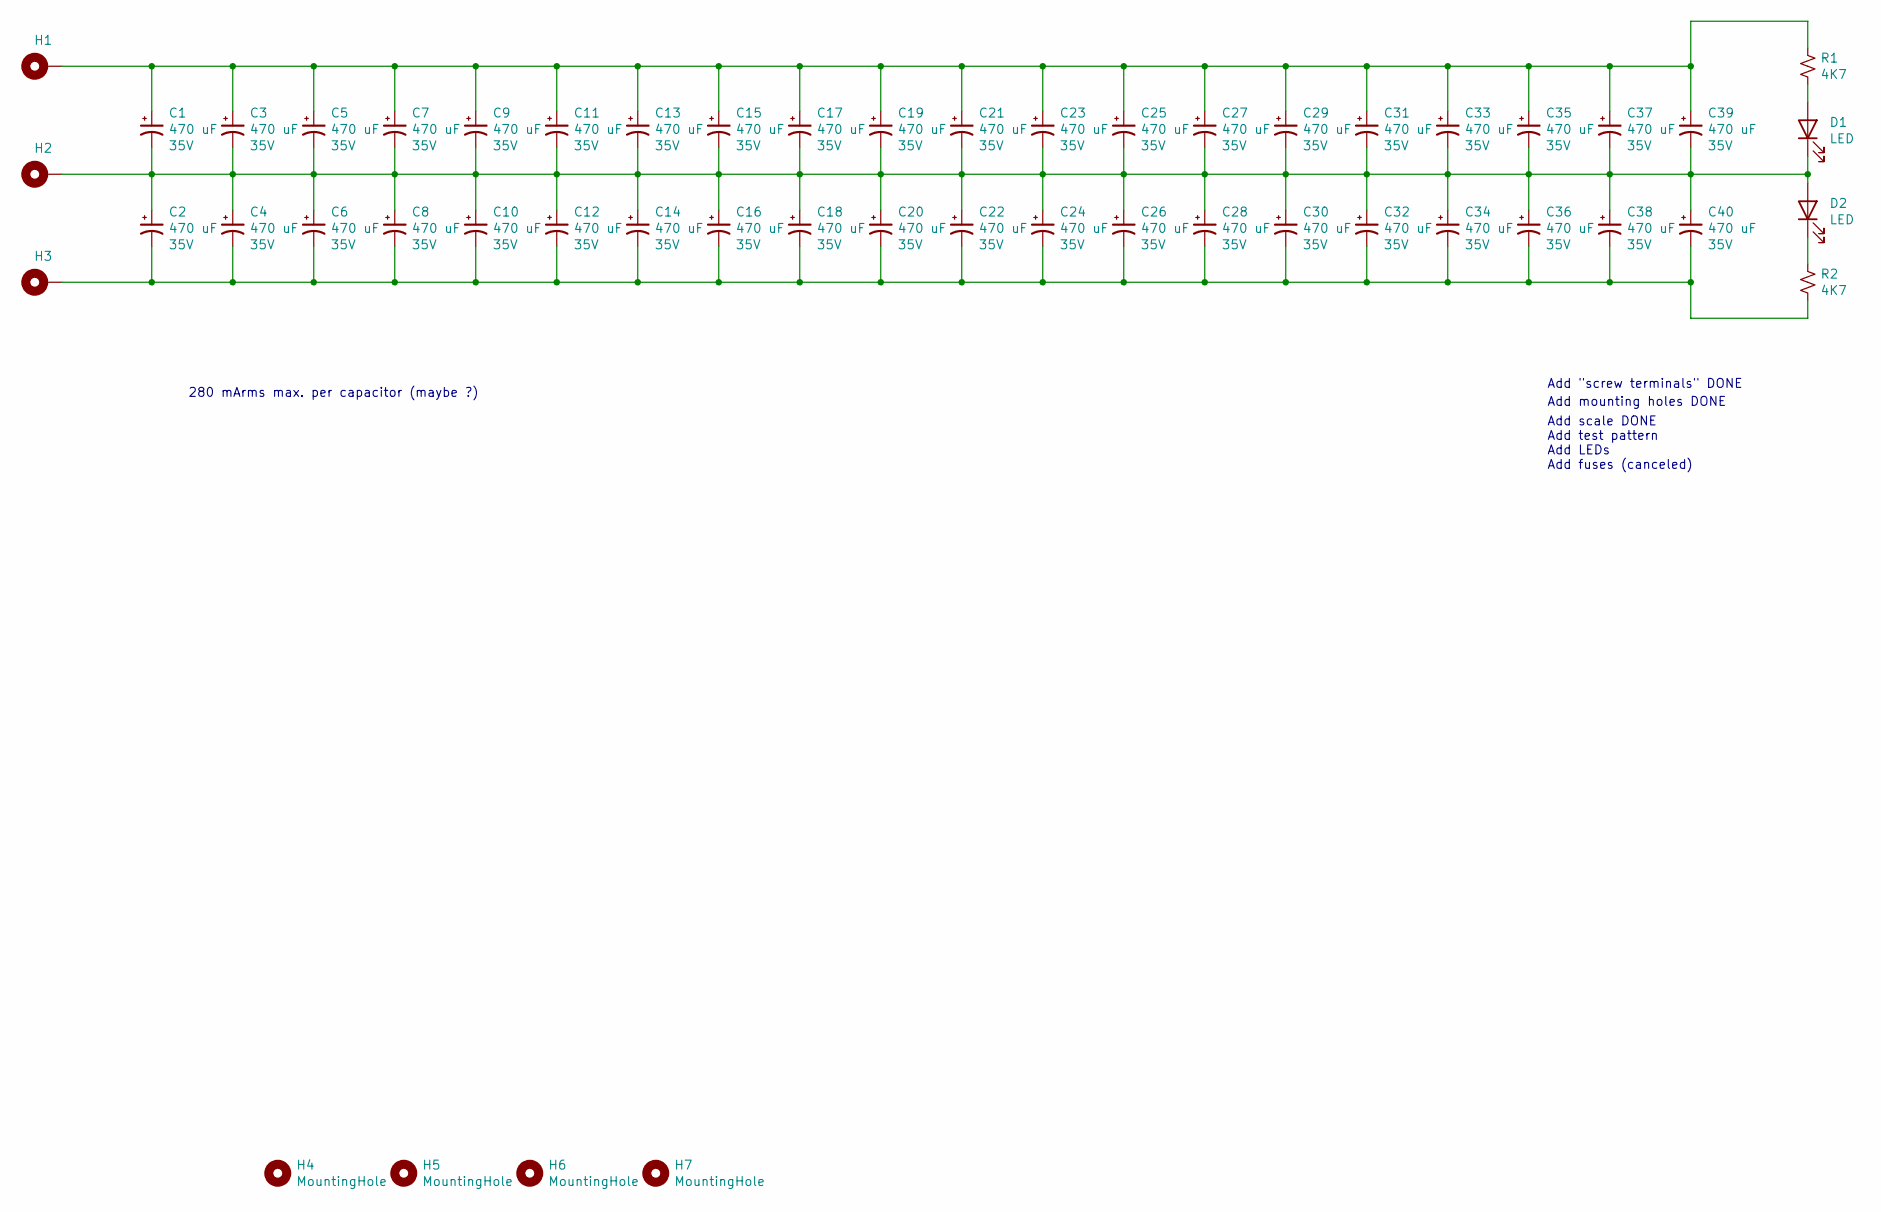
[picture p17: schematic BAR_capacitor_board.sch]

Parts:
C1, C2, C3, C4, C5, C6, C7, C8, C9, C10, C11, C12, C13, C14, C15, C16, C17, C18, C19, C20, C21, C22, C23, C24, C25, C26, C27, C28, C29, C30, C31, C32, C33, C34, C35, C36, C37, C38, C39, C40: 470 uF; CP_Elec_10x10.5; Max Voltage 35V
D1, D2: LED; LED_1206_3216Metric_Castellated
H1, H2, H3: MountingHole_Pad; SMD_REDCUBE_M4
H4, H5, H6, H7: MountingHole; MountingHole_3.2mm_M3_ISO14580_Pad
R1, R2: 4K7; R_1206_3216Metric

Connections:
unnamed: C1.1, C3.1, C5.1, C7.1, C9.1, C11.1, C13.1, C15.1, C17.1, C19.1, C21.1, C23.1, C25.1, C27.1, C29.1, C31.1, C33.1, C35.1, C37.1, C39.1, H1.1, R1.1
unnamed: C1.2, C2.1, C3.2, C4.1, C5.2, C6.1, C7.2, C8.1, C9.2, C10.1, C11.2, C12.1, C13.2, C14.1, C15.2, C16.1, C17.2, C18.1, C19.2, C20.1, C21.2, C22.1, C23.2, C24.1, C25.2, C26.1, C27.2, C28.1, C29.2, C30.1, C31.2, C32.1, C33.2, C34.1, C35.2, C36.1, C37.2, C38.1, C39.2, C40.1, D1.1 (K), D2.2 (A), H2.1
unnamed: C2.2, C4.2, C6.2, C8.2, C10.2, C12.2, C14.2, C16.2, C18.2, C20.2, C22.2, C24.2, C26.2, C28.2, C30.2, C32.2, C34.2, C36.2, C38.2, C40.2, H3.1, R2.2
unnamed: D1.2 (A), R1.2
unnamed: D2.1 (K), R2.1

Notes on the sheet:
Add mounting holes DONE
Add "screw terminals" DONE
280 mArms max. per capacitor (maybe ?)
Add scale DONE Add test pattern Add LEDs Add fuses (canceled)

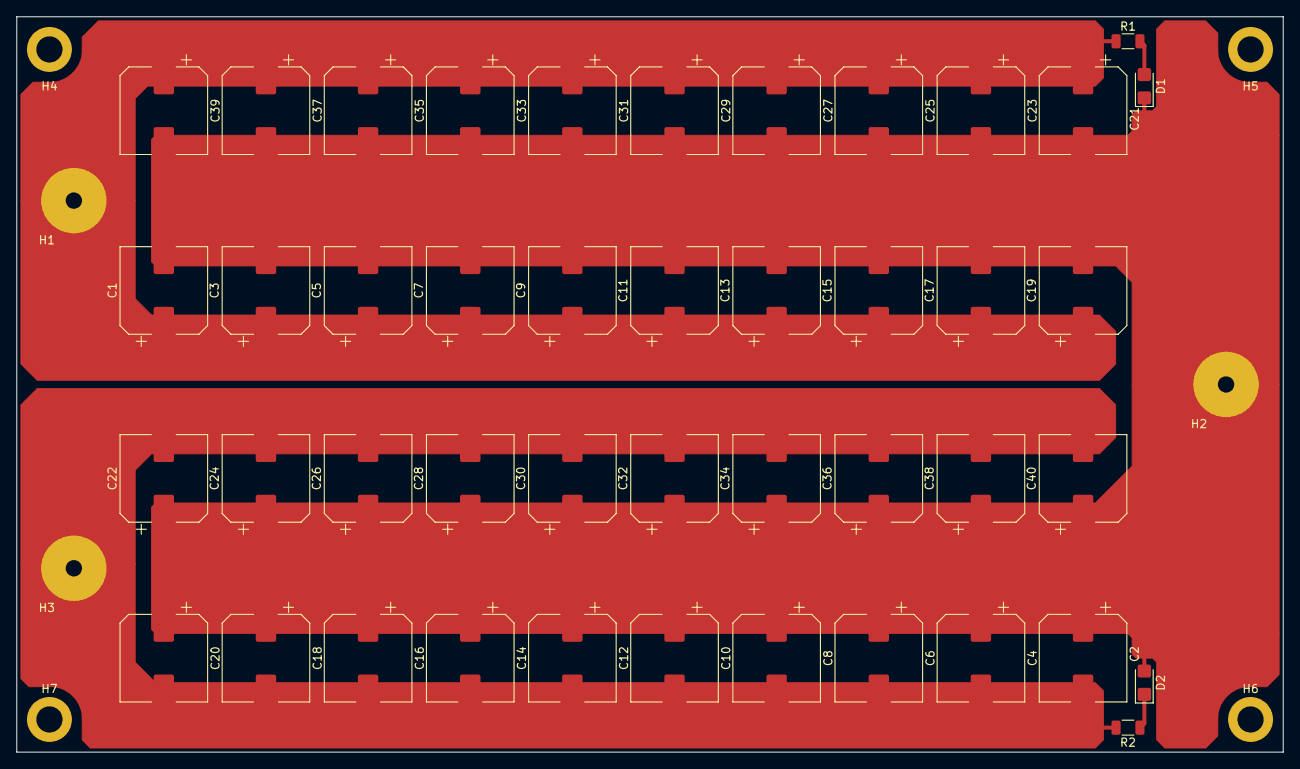
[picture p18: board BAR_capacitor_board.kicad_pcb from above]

Board: 2 copper layers, 155.0 x 90.0 mm, 51 parts (0 on the bottom side), 5 nets.

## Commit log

2022-01-06 Added Files
    First real commit, adding all the files
    [AC&DC_Frontends.SchDoc, Bidir_Active_Rectifier-Main_Board.PrjPcb, Bidir_Active_Rectifier_Library.PcbLib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]
2022-01-06 Edited Readme.md and updated project file
    [Bidir_Active_Rectifier-Main_Board.PrjPcb]
2022-01-07 Finished logical groupings
    And fixed some footprints
    [Bidir_Active_Rectifier_Library.SchLib, Internal_Supplies_1.SchDoc, MCU.SchDoc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]
2022-01-08 Rough placement of the power section done
    Design rules added as per OSHPark rules (JLCPCB less stringent). Net classes created and the net attribution for them was started.
    [Bidir_Active_Rectifier_Library.PcbLib, Power_Stage.SchDoc]
2022-01-11 Added most pours for the power section
    [Bidir_Active_Rectifier_Library.PcbLib, Bidir_Active_Rectifier_Library.SchLib, Gate_Drive.SchDoc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]
2022-01-13 Fixed classes. Improved board outlines. Changed some placement
    [AC&DC_Frontends.SchDoc, Bidir_Active_Rectifier-Main_Board.PrjPcb, Bidir_Active_Rectifier_Library.PcbLib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]
2022-01-14 Lower section of board *almost* finished
    Placed and routed
    [AC&DC_Frontends.SchDoc, Internal_Supplies_1.SchDoc, Protection_Logic.SchDoc]
2022-01-17 Finalized the lower portion
    [AC&DC_Frontends.SchDoc, Gate_Drive.SchDoc]
2022-01-17 Started upper portion
    [Gate_Drive.SchDoc, Internal_Supplies_1.SchDoc, MCU_Analog_1.SchDoc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]
2022-01-18 Changed connectors to SMD
    [Bidir_Active_Rectifier_Library.PcbLib, Bidir_Active_Rectifier_Library.SchLib, MCU.SchDoc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]
2022-01-20 Advanced placement and routing of upper portion
    [Control_Loop.SchDoc, Internal_Supplies_1.SchDoc, MCU.SchDoc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]
2022-01-21 Advanced upper portion
    Upper right almost finished. Board dimensions final at 95mm x 135mm
    [Internal_Supplies_1.SchDoc, Internal_Supplies_2.SchDoc, MCU.SchDoc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]
2022-01-21 Analog section and silk left
    Almost everything else is done
    [Bidir_Active_Rectifier_Library.PcbLib, Bidir_Active_Rectifier_Library.SchLib, Gate_Drive.SchDoc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]
2022-01-24 Improved analog section, changed some footprints to clear some errors
    [Bidir_Active_Rectifier_Library.PcbLib, Bidir_Active_Rectifier_Library.SchLib, Control_Loop.SchDoc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]
2022-01-25 Finished
    Silkscreen is all cute and everything.
    [Bidir_Active_Rectifier_Library.PcbLib]
2022-01-25 Changed some footprints and parameters to export the BOM
    [BOM.xlsx, Bidir_Active_Rectifier-Main_Board.PrjPcb, Control_Loop.SchDoc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]
2022-01-26 Comparator and annotation change
    Comparators changed to use the much more popular SOT-23-5 footprint. Whole board reannotated for convenience. Re-exported BOM and PDF.
    [AC&DC_Frontends.SchDoc, BOM.xlsx, Bidir_Active_Rectifier_Library.PcbLib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]
2022-01-26 Simplified path
    [AC&DC_Frontends.SchDoc, BOM.xlsx, Bidir_Active_Rectifier-Main_Board.PrjPcb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]
2022-01-26 Exported gerber files
    Fixed 33 pF caps for the BOM as well.
    [BOM.xlsx, Bidir_Active_Rectifier-Main_Board.PrjPcb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]
2022-04-14 Added files for Capacitor and Mains interface boards
    Those were made using KiCAD
    [AC&DC_Frontends.SchDoc, BAR_capacitor_board.kicad_pcb, BAR_capacitor_board.sch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]
2022-05-09 Added TODO
    Add teardrops!
    [MCU.SchDoc]
